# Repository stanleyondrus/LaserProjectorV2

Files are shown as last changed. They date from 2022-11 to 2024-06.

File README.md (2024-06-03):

(https://stanleyprojects.com/projects/laserprojector_v2/)
(https://stanleyprojects.com/projects/laserprojector_v2/)

## Introduction
LaserProjector V2 is a battery-powered, ESP32-based laser XY scanner using stepper motors to deflect the beam. It has auto-homing functionality, and can be controlled wirelessly (Wi-Fi & Bluetooth).

## Features
- Hybrid Wi-Fi operation mode (STA & AP)
- Webserver GUI with custom WebSocket protocol
- Concurrent multi-user control
- Automatic/Manual/External scanning mode
- Parallel auto-homing
- Battery-powered

## Links
- [Documentation [stanleyprojects.com]](https://stanleyprojects.com/projects/laserprojector_v2/)
- [Article [hackaday.com]](https://hackaday.com/2022/11/02/laser-project-relies-on-steppers-rather-than-galvanometers/)
- [Video [youtube.com]](https://youtu.be/w1O48Ysdiiw)
- [Project [hackaday.io]](https://hackaday.io/project/188046-laserprojector-v2)
- [Project [hackster.io]](https://www.hackster.io/stanleyprojects/laserprojector-v2-fa77cf)

## Design




## How to build your own release
### Prerequisites
- Visual Studio Code with PlatformIO extension
- 3.3V USB to Serial (e.g. FT232RL)
### Building
1. Open __*firmware/src*__ folder in VSCode
2. In __*firmware/src/src/main.cpp*__ you can sustomize SSID and PASSWORD for Wi-Fi STA mode:
```cpp
const char* ssid = "<your_ssid>";
const char* password = "<your_pass>";
```
3. In __*firmware/src/platformio.ini*__ set the correct *_upload_port_*, or remove to auto-detect.

4. Build and upload the filesystem
    - PlatformIO > esp32serial > Platform > Build Filesystem Image
    - PlatformIO > esp32serial > Platform > Upload Filesystem Image

5. Build and upload the firmware
    - PlatformIO > esp32serial > General > Upload

## Pre-built binaries
The binary is fully contained (bootloader, firmware, and filesystem), so it can be flashed to address 0x0.

The easiest way is to use this web tool: https://stanleyprojects.com/projects/laserprojector_v2/install

After the firmware is loaded, any subsequent updates can be done OTA in browser by visiting _http://\<esp32-ip-address\>/update_

|Version|Firmware|
|-|-|
|0.1|[LaserProjectorV2_firmware_v0.1.bin](https://github.com/stanleyondrus/LaserProjectorV2/releases/download/v0.1/LaserProjectorV2_v0.1.bin)|

## Credits
- [A Beginner's Guide to the ESP8266](https://tttapa.github.io/ESP8266/Chap01%20-%20ESP8266.html)
- [ElegantOTA](https://github.com/ayushsharma82/ElegantOTA)
- [StepperDriver](https://github.com/laurb9/StepperDriver)

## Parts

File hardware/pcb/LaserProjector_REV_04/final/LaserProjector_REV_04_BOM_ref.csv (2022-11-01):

Ref | Value | MPN | Manufacturer | Package | Datasheet
C1 | 2.2uF | GRM188R61H225KE11D | Murata Electronics | 0603 | https://datasheet.lcsc.com/lcsc/1912111437_Murata-Electronics-GRM188R61H225KE11D_C162273.pdf
C2 | 22uF | EEEHBH220UAP | Panasonic | SMD (6.3x5.8mm) | https://datasheet.lcsc.com/lcsc/1912111437_PANASONIC-EEEHBH220UAP_C401821.pdf
C3 | 10uF | CL21A106KAYNNNE | Samsung Electro-Mechanics | 0805 | https://datasheet.lcsc.com/szlcsc/1811121310_Samsung-Electro-Mechanics-CL21A106KAYNNNE_C15850.pdf
C4 | 22uF | C2012X5R0J226MT000N | TDK | 0805 | https://datasheet.lcsc.com/szlcsc/1912111437_TDK-C2012X5R0J226MT000N_C329961.pdf
C5 | 1nF | GCM155R71H102KA37D | Murata Electronics | 0402 | https://datasheet.lcsc.com/lcsc/1811081510_Murata-Electronics-GCM155R71H102KA37D_C126532.pdf
C6 | 22nF | GRM155R71E223JA61D | Murata Electronics | 0402 | https://datasheet.lcsc.com/lcsc/1912111437_Murata-Electronics-GRM155R71E223JA61D_C426639.pdf
C7 | 100nF | CC0402KRX7R7BB104 | Yageo | 0402 | https://www.yageo.com/upload/media/product/productsearch/datasheet/mlcc/UPY-GPHC_X7R_6.3V-to-50V_18.pdf
C8 | 2.2uF | GRM188R61H225KE11D | Murata Electronics | 0603 | https://datasheet.lcsc.com/lcsc/1912111437_Murata-Electronics-GRM188R61H225KE11D_C162273.pdf
C9 | 22uF | EEEHBH220UAP | Panasonic | SMD (6.3x5.8mm) | https://datasheet.lcsc.com/lcsc/1912111437_PANASONIC-EEEHBH220UAP_C401821.pdf
C10 | 1nF | GCM155R71H102KA37D | Murata Electronics | 0402 | https://datasheet.lcsc.com/lcsc/1811081510_Murata-Electronics-GCM155R71H102KA37D_C126532.pdf
C11 | 22nF | GRM155R71E223JA61D | Murata Electronics | 0402 | https://datasheet.lcsc.com/lcsc/1912111437_Murata-Electronics-GRM155R71E223JA61D_C426639.pdf
J1 | J_Molex-PicoBlade-4P-P1.25mm | 0530470410 | Molex | Through Hole, P=1.25mm | https://www.molex.com/pdm_docs/sd/530470410_sd.pdf
J2 | JST-XH-B2B | B2B-XH-A(LF)(SN) | JST Sales America | Through Hole, P=2.5mm | http://www.jst-mfg.com/product/pdf/eng/eXH.pdf
J3 | J_Molex-PicoBlade-3P-P1.25mm | 0530470310 | Molex | Through Hole, P=1.25mm | https://www.molex.com/pdm_docs/sd/530470310_sd.pdf
J4 | J_Molex-PicoBlade-3P-P1.25mm | 0530470310 | Molex | Through Hole, P=1.25mm | https://www.molex.com/pdm_docs/sd/530470310_sd.pdf
J5 | JST-XH-B4B | B4B-XH-A(LF)(SN) | JST Sales America | Through Hole, P=2.5mm | https://datasheet.lcsc.com/szlcsc/1811151545_JST-Sales-America-B4B-XH-A-LF-SN_C144395.pdf
J7 | J_Molex-PicoBlade-4P-P1.25mm | 0530470410 | Molex | Through Hole, P=1.25mm | https://www.molex.com/pdm_docs/sd/530470410_sd.pdf
L1 | 2.2uH | VLCF4020T-2R2N1R7 | TDK | 4x4x2mm | https://datasheet.lcsc.com/szlcsc/1810211523_TDK-VLCF4020T-2R2N1R7_C136245.pdf
Q1 | NCE2060K | NCE2060K | Wuxi NCE Power Semiconductor | TO-252-2L | http://www.ncepower.com/Upload/MOSFET/NCE2060Kdatasheet-15115513193.pdf
Q2 | NMOS | NTR4501NT1G | ON Semicon | SOT-23 | https://datasheet.lcsc.com/szlcsc/1810301530_ON-Semicon-NTR4501NT1G_C85416.pdf
R1 | 0.2R | WW25WR200FTL | Walsin Tech Corp | 2512 | https://datasheet.lcsc.com/lcsc/1912211104_Walsin-Tech-Corp-WW25WR200FTL_C470051.pdf
R2 | 47k | RC0402FR-0747KL | Yageo | 0402 | https://www.mouser.dk/datasheet/2/447/PYu_RC_Group_51_RoHS_L_10-1664068.pdf
R3 | 0.2R | WW25WR200FTL | Walsin Tech Corp | 2512 | https://datasheet.lcsc.com/lcsc/1912211104_Walsin-Tech-Corp-WW25WR200FTL_C470051.pdf
R4 | 100k | RT0402BRE07100KL | YAGEO | 0402 | https://datasheet.lcsc.com/lcsc/1810241324_YAGEO-RT0402BRE07100KL_C136979.pdf
R5 | 1k | 0402WGF1001TCE | Uniroyal Elec | 0402 | https://datasheet.lcsc.com/szlcsc/1811132311_Uniroyal-Elec-0402WGF1001TCE_C11702.pdf
R6 | 1k | 0402WGF1001TCE | Uniroyal Elec | 0402 | https://datasheet.lcsc.com/szlcsc/1811132311_Uniroyal-Elec-0402WGF1001TCE_C11702.pdf
R7 | 10k | RT0402BRD0710KL | YAGEO | 0402 | https://datasheet.lcsc.com/szlcsc/1810241334_YAGEO-RT0402BRD0710KL_C190095.pdf
R8 | 10k | RT0402BRD0710KL | YAGEO | 0402 | https://datasheet.lcsc.com/szlcsc/1810241334_YAGEO-RT0402BRD0710KL_C190095.pdf
R9 | 0.2R | WW25WR200FTL | Walsin Tech Corp | 2512 | https://datasheet.lcsc.com/lcsc/1912211104_Walsin-Tech-Corp-WW25WR200FTL_C470051.pdf
R10 | 47k | RC0402FR-0747KL | Yageo | 0402 | https://www.mouser.dk/datasheet/2/447/PYu_RC_Group_51_RoHS_L_10-1664068.pdf
R11 | 0.2R | WW25WR200FTL | Walsin Tech Corp | 2512 | https://datasheet.lcsc.com/lcsc/1912211104_Walsin-Tech-Corp-WW25WR200FTL_C470051.pdf
R12 | 100k | RT0402BRE07100KL | YAGEO | 0402 | https://datasheet.lcsc.com/lcsc/1810241324_YAGEO-RT0402BRE07100KL_C136979.pdf
R13 | 1k | 0402WGF1001TCE | Uniroyal Elec | 0402 | https://datasheet.lcsc.com/szlcsc/1811132311_Uniroyal-Elec-0402WGF1001TCE_C11702.pdf
R14 | 1k | 0402WGF1001TCE | Uniroyal Elec | 0402 | https://datasheet.lcsc.com/szlcsc/1811132311_Uniroyal-Elec-0402WGF1001TCE_C11702.pdf
R15 | 10k | RT0402BRD0710KL | YAGEO | 0402 | https://datasheet.lcsc.com/szlcsc/1810241334_YAGEO-RT0402BRD0710KL_C190095.pdf
SW1 | EVPAA602W | EVPAA602W | Panasonic | SMD | https://datasheet.lcsc.com/szlcsc/1809192044_PANASONIC-EVPAA602W_C79148.pdf
SW2 | EVPAA602W | EVPAA602W | Panasonic | SMD | https://datasheet.lcsc.com/szlcsc/1809192044_PANASONIC-EVPAA602W_C79148.pdf
U1 | TPS62162DSG | TPS62162DSG | Texas Instruments | WSON-8 (2x2mm) | https://datasheet.lcsc.com/lcsc/1806070425_Texas-Instruments-TPS62162DSGR_C40256.pdf
U2 | STSPIN220 | STSPIN220 | STMicroelectronics | VFQFPN 3x3x1.0 | www.st.com/resource/en/datasheet/stspin220.pdf
U3 | STSPIN220 | STSPIN220 | STMicroelectronics | VFQFPN 3x3x1.0 | www.st.com/resource/en/datasheet/stspin220.pdf
U4 | ESP32 |  |  |  | https://www.espressif.com/sites/default/files/documentation/esp32-wroom-32_datasheet_en.pdf

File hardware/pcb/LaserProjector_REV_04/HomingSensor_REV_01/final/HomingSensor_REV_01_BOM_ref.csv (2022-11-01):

Ref | Value | MPN | Manufacturer | Package | Datasheet
C1 | 10nF | CL05B103KB5NNNC | Samsung Electro-Mechanics | 0402 | https://datasheet.lcsc.com/szlcsc/1810191223_Samsung-Electro-Mechanics-CL05B103KB5NNNC_C15195.pdf
R1 | 100R | AC0402FR-07100RL | Yageo | 0402 | https://eu.mouser.com/datasheet/2/447/PYu-AC_51_RoHS_L_7-1714230.pdf
R2 | 220R | 0402WGF2200TCE | UNI-ROYAL | 0402 | https://datasheet.lcsc.com/szlcsc/1811011214_UNI-ROYAL-Uniroyal-Elec-0402WGF2200TCE_C25091.pdf
U1 | QRE1113 |  |  |  | http://www.onsemi.com/pub/Collateral/QRE1113-D.PDF

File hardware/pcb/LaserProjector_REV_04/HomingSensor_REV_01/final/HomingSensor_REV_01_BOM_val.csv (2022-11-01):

Qty | Designator | Value | Datasheet | MPN | Manufacturer | Package
1 | C1 | 10nF | https://datasheet.lcsc.com/szlcsc/1810191223_Samsung-Electro-Mechanics-CL05B103KB5NNNC_C15195.pdf | Samsung Electro-Mechanics | CL05B103KB5NNNC | 0402
1 | R1 | 100R | https://eu.mouser.com/datasheet/2/447/PYu-AC_51_RoHS_L_7-1714230.pdf | Yageo | AC0402FR-07100RL | 0402
1 | R2 | 220R | https://datasheet.lcsc.com/szlcsc/1811011214_UNI-ROYAL-Uniroyal-Elec-0402WGF2200TCE_C25091.pdf | UNI-ROYAL | 0402WGF2200TCE | 0402
1 | U1 | QRE1113 | http://www.onsemi.com/pub/Collateral/QRE1113-D.PDF

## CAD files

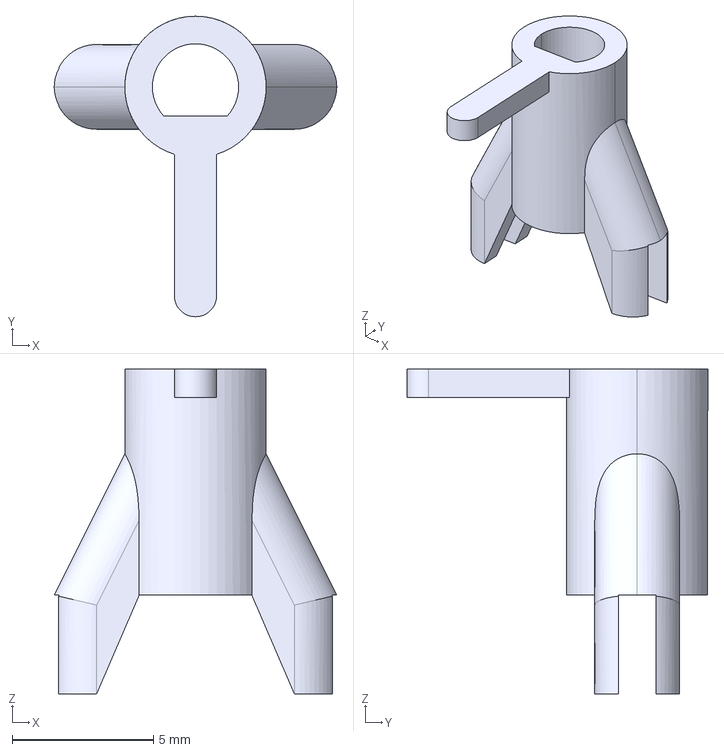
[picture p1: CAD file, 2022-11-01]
hardware/cad/MirrorHolder.STEP
10.0 x 10.6 x 11.5 mm

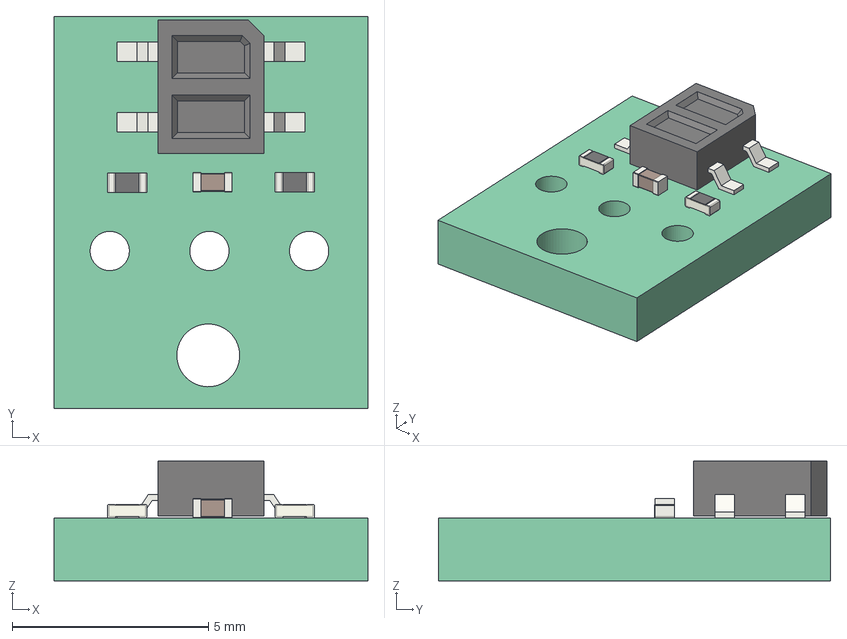
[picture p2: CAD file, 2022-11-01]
hardware/pcb/LaserProjector_REV_04/HomingSensor_REV_01/final/HomingSensor_REV_01.step
8.00 x 10.0 x 3.05 mm
Local_CS_25fb
Pcb_25fb
PCB_Sketch_25fb
U1_OnSemi_CASE100CY_5FA408A3
R2_R_0402_1005Metric_5FA4088F
R1_R_0402_1005Metric_5FA40D70
C1_C_0402_1005Metric_5FA4085A

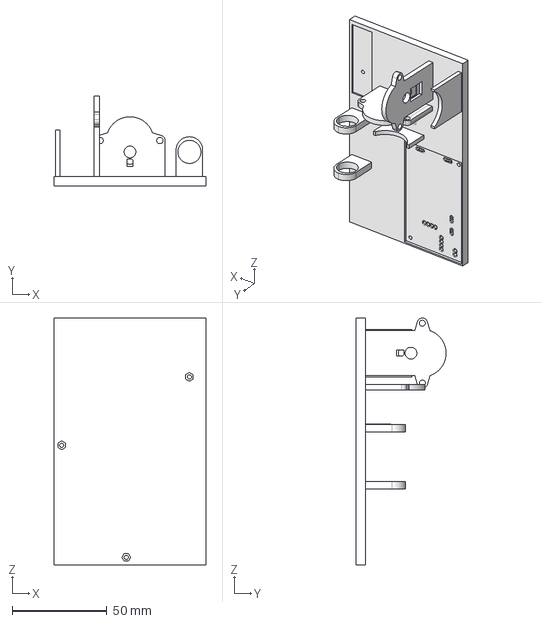
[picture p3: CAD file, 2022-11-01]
hardware/cad/ScannerHolder.STEP
80.0 x 47.5 x 130.0 mm

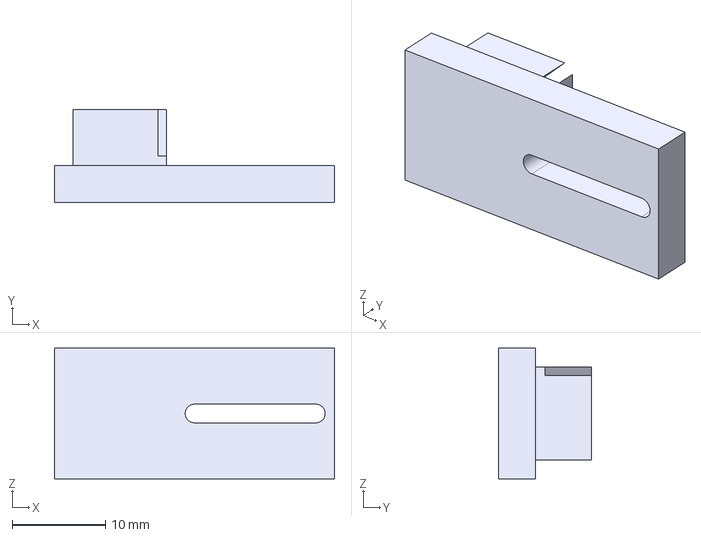
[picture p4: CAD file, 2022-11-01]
hardware/cad/BeamAligner.STEP
30.0 x 10.0 x 14.0 mm

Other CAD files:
hardware/cad/BeamAligner.STL
hardware/cad/MirrorHolder.STL
hardware/cad/ScannerHolder.STL

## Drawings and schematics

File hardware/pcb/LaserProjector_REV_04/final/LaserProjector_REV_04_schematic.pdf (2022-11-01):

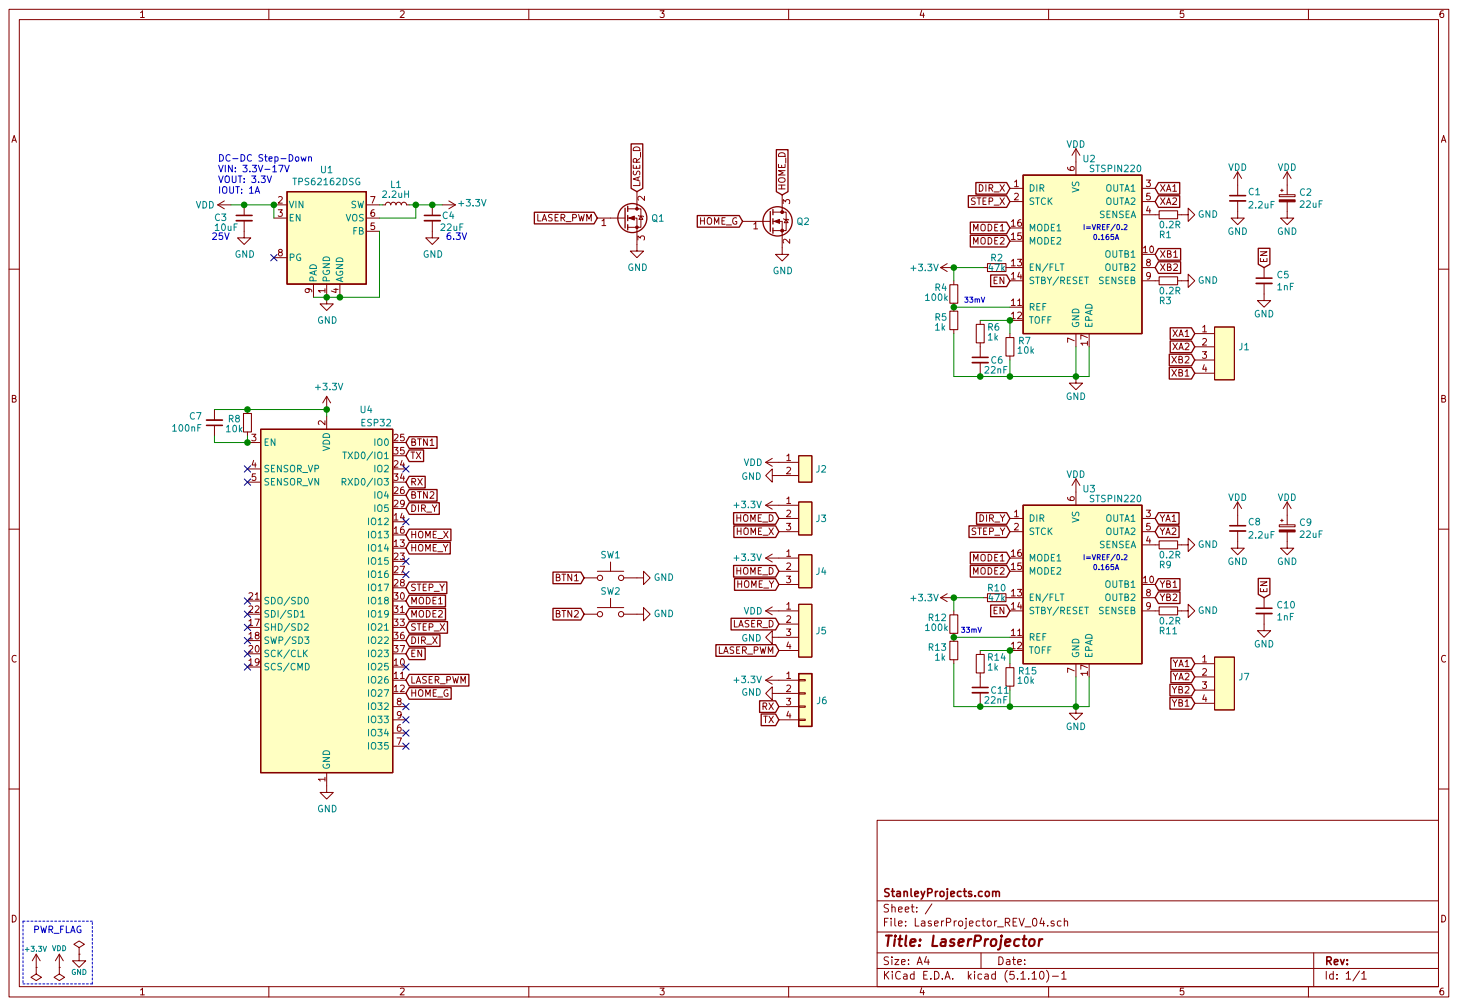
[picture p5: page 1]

DC-DC Step-Down VIN: 3.3V-17V

4 FB 5 VOS 6 SW 7 PG 8 PAD

2 SCK/CLK 20 SDO/SD0 21 SDI/SD1 22
TXHOME_Y HOME_G

File: LaserProjector_REV_04.sch Sheet: / StanleyProjects.com

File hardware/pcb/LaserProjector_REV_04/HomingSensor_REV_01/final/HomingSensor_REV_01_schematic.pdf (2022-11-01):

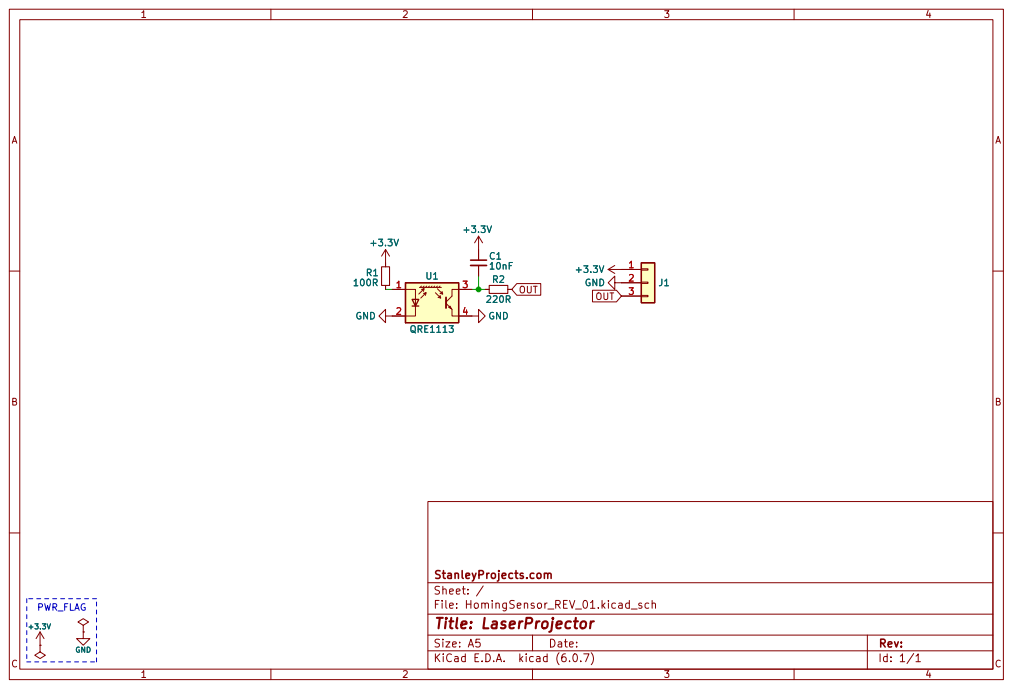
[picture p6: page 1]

File: HomingSensor_REV_01.kicad_sch Sheet: / StanleyProjects.com

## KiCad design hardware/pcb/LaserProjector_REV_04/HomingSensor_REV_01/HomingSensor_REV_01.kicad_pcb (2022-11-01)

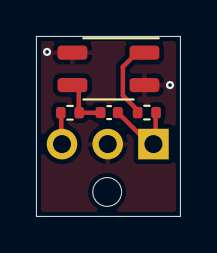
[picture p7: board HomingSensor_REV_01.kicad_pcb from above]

Board: 2 copper layers, 8.0 x 10.0 mm, 5 parts (1 on the bottom side), 5 nets.

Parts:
C1: 10nF; C_0402_1005Metric
J2: Connector; PinSocket_1x03_P2.54mm_Vertical
R1: 100R; R_0402_1005Metric
R2: 220R; R_0402_1005Metric
U1: QRE1113; OnSemi_CASE100CY

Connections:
+3V3: C1.1, J2.1, R1.2
GND: J2.2, U1.2, U1.4
unnamed: C1.2, R2.2, U1.3
unnamed: R1.1, U1.1
OUT: J2.3, R2.1

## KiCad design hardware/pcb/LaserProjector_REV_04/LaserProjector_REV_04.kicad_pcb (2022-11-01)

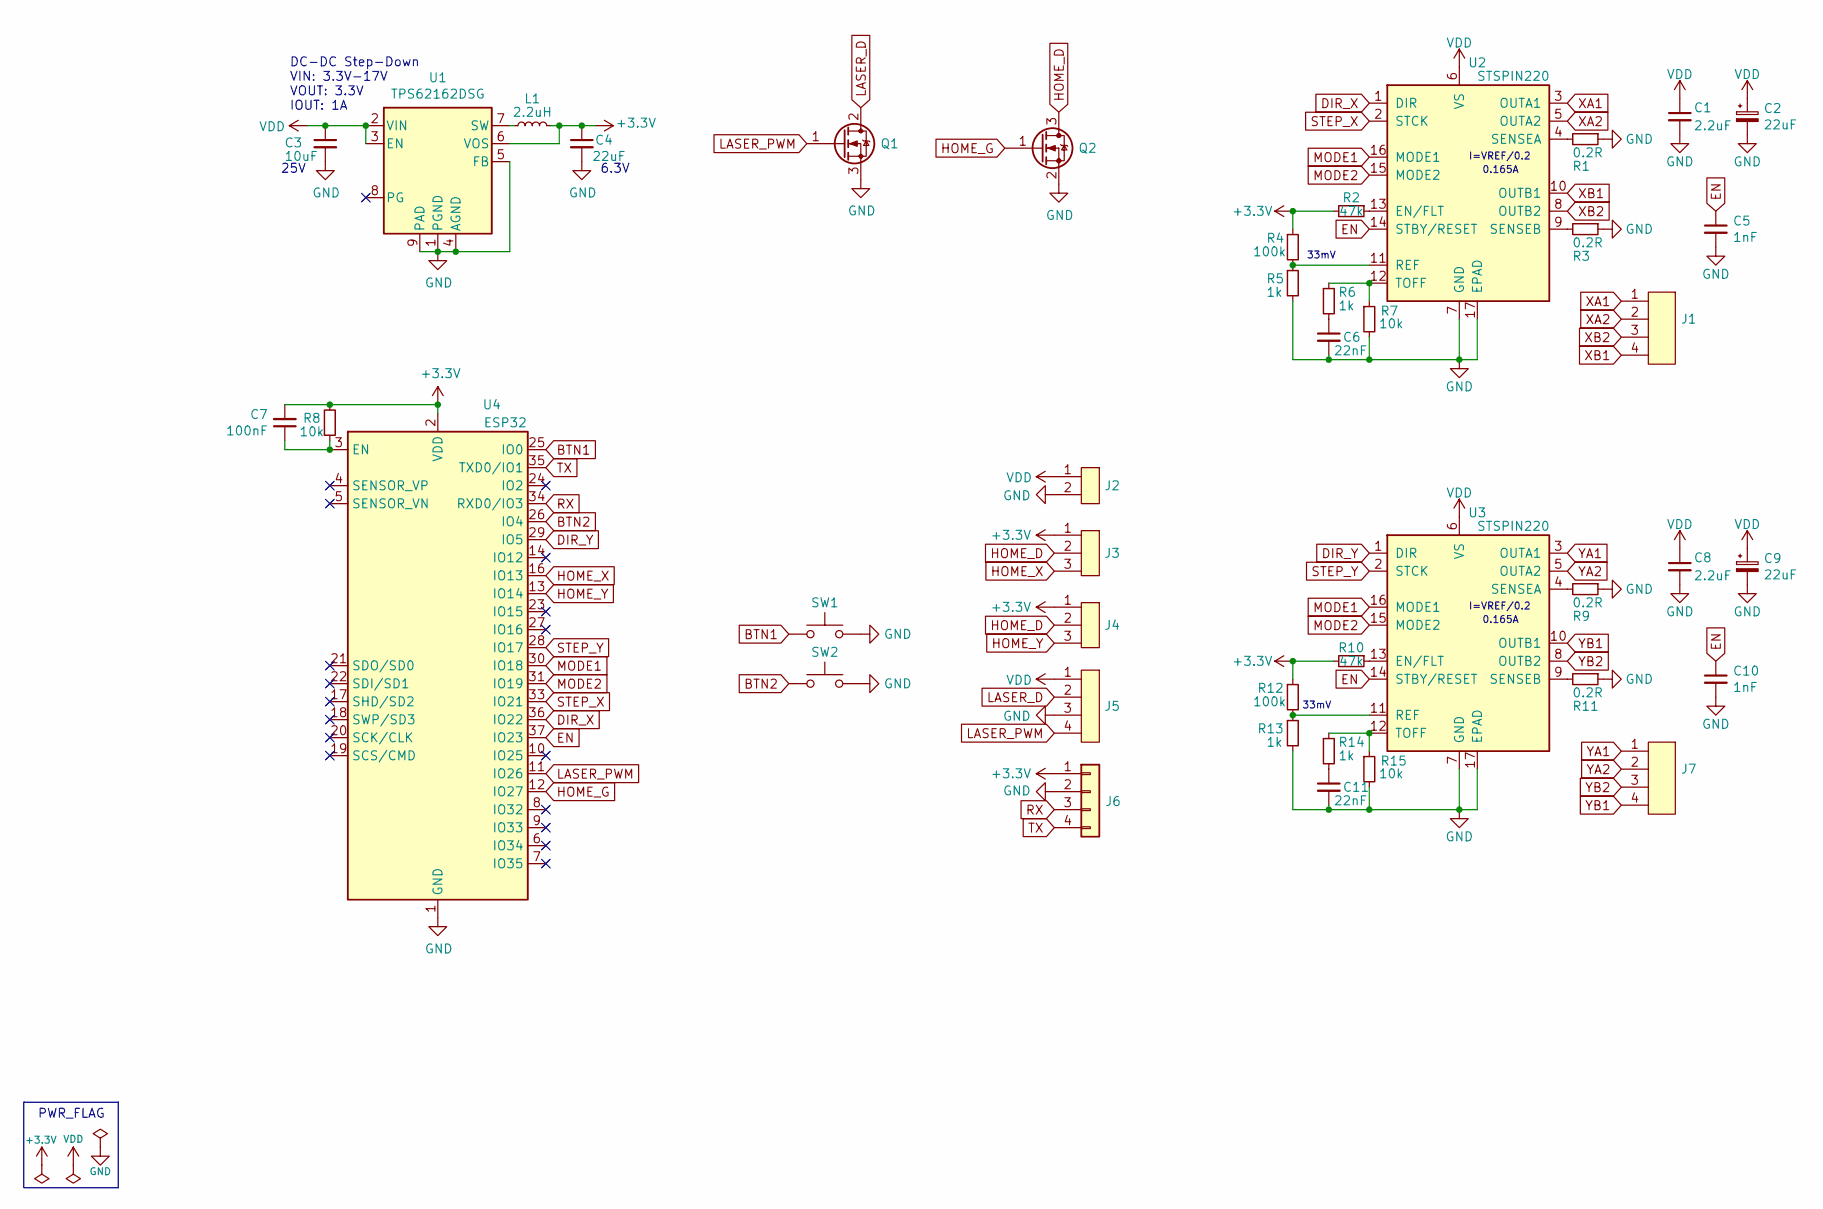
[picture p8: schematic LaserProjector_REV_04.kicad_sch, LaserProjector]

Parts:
C1, C8: 2.2uF; C_0603_1608Metric; MPN GRM188R61H225KE11D
C2, C9: 22uF; CP_Elec_6.3x5.8; MPN EEEHBH220UAP
C3: 10uF; C_0805_2012Metric; MPN CL21A106KAYNNNE
C4: 22uF; C_0805_2012Metric; MPN C2012X5R0J226MT000N
C5, C10: 1nF; C_0402_1005Metric; MPN GCM155R71H102KA37D
C6, C11: 22nF; C_0402_1005Metric; MPN GRM155R71E223JA61D
C7: 100nF; C_0402_1005Metric; MPN CC0402KRX7R7BB104
J1, J7: J_Molex-PicoBlade-4P-P1.25mm; Molex_PicoBlade_53047-0410_1x04_P1.25mm_Vertical; MPN 0530470410
J2: JST-XH-B2B; JST_XH_B2B-XH-A_1x02_P2.50mm_Vertical; MPN B2B-XH-A(LF)(SN)
J3, J4: J_Molex-PicoBlade-3P-P1.25mm; Molex_PicoBlade_53047-0310_1x03_P1.25mm_Vertical; MPN 0530470310
J5: JST-XH-B4B; JST_XH_B4B-XH-A_1x04_P2.50mm_Vertical; MPN B4B-XH-A(LF)(SN)
J6: Conn_01x04; PinHeader_1x04_P2.54mm_Vertical
L1: 2.2uH; VLCF4020; MPN VLCF4020T-2R2N1R7
Q1: NCE2060K; TO-252-2; MPN NCE2060K
Q2: NMOS; SOT-23; MPN NTR4501NT1G
R1, R3, R9, R11: 0.2R; R_2512_6332Metric; MPN WW25WR200FTL
R2, R10: 47k; R_0402_1005Metric; MPN RC0402FR-0747KL
R4, R12: 100k; R_0402_1005Metric; MPN RT0402BRE07100KL
R5, R6, R13, R14: 1k; R_0402_1005Metric; MPN 0402WGF1001TCE
R7, R8, R15: 10k; R_0402_1005Metric; MPN RT0402BRD0710KL
SW1, SW2: EVPAA602W; SW_EVPAA; MPN EVPAA602W
U1: TPS62162DSG; WSON-8-1EP_2x2mm_P0.5mm_EP0.9x1.6mm_ThermalVias; MPN TPS62162DSG
U2, U3: STSPIN220; MPN STSPIN220
U4: ESP32; ESP32-WROOM-32

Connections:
+3V3: C4.1, C7.2, J3.1, J4.1, J6.1, L1.2, R2.2, R4.1, R8.2, R10.2, R12.1, U1.6 (VOS), U4.2 (VDD)
BTN1: SW1.1, SW1.3, U4.25 (IO0); also elsewhere on the board
BTN2: SW2.1, SW2.3, U4.26 (IO4); also elsewhere on the board
DIR_X: U2.1 (DIR), U4.36 (IO22)
DIR_Y: U3.1 (DIR), U4.29 (IO5)
EN: C5.1, C10.1, U2.14 (STBY/RESET), U3.14 (STBY/RESET), U4.37 (IO23)
GND: C1.2, C2.2, C3.2, C4.2, C5.2, C6.2, C8.2, C9.2, C10.2, C11.2, J2.2, J5.3, J6.2, Q1.3 (S), Q2.2 (S), R1.1, R3.1, R5.2, R7.2, R9.1, R11.1, R13.2, R15.2, SW1.2, SW1.4, SW2.2, SW2.4, U1.1 (PGND), U1.4 (AGND), U1.5 (FB), U1.8 (PG), U1.9 (PAD), U2.7 (GND), U2.17 (EPAD), U3.7 (GND), U3.17 (EPAD), U4.1 (GND), U4.15 (GND), U4.38 (GND), U4.39 (GND); also elsewhere on the board
HOME_D: J3.2, J4.2, Q2.3 (D)
HOME_G: Q2.1 (G), U4.12 (IO27)
HOME_X: J3.3, U4.16 (IO13)
HOME_Y: J4.3, U4.13 (IO14)
LASER_D: J5.2, Q1.2 (D)
LASER_PWM: J5.4, Q1.1 (G), U4.11 (IO26)
MODE1: U2.16 (MODE1), U3.16 (MODE1), U4.30 (IO18)
MODE2: U2.15 (MODE2), U3.15 (MODE2), U4.31 (IO19)
unnamed: C6.1, R6.2
unnamed: C7.1, R8.1, U4.3 (EN)
unnamed: C11.1, R14.2
unnamed: L1.1, U1.7 (SW)
unnamed: R1.2, U2.4 (SENSEA)
unnamed: R2.1, U2.13 (EN/FLT)
unnamed: R3.2, U2.9 (SENSEB)
unnamed: R4.2, R5.1, U2.11 (REF)
unnamed: R6.1, R7.1, U2.12 (TOFF)
unnamed: R9.2, U3.4 (SENSEA)
unnamed: R10.1, U3.13 (EN/FLT)
unnamed: R11.2, U3.9 (SENSEB)
unnamed: R12.2, R13.1, U3.11 (REF)
unnamed: R14.1, R15.1, U3.12 (TOFF)
RX: J6.3, U4.34 (RXD0/IO3)
STEP_X: U2.2 (STCK), U4.33 (IO21)
STEP_Y: U3.2 (STCK), U4.28 (IO17)
TX: J6.4, U4.35 (TXD0/IO1)
VDD: C1.1, C2.1, C3.1, C8.1, C9.1, J2.1, J5.1, U1.2 (VIN), U1.3 (EN), U2.6 (VS), U3.6 (VS)
XA1: J1.1, U2.3 (OUTA1)
XA2: J1.2, U2.5 (OUTA2)
XB1: J1.4, U2.10 (OUTB1)
XB2: J1.3, U2.8 (OUTB2)
YA1: J7.1, U3.3 (OUTA1)
YA2: J7.2, U3.5 (OUTA2)
YB1: J7.4, U3.10 (OUTB1)
YB2: J7.3, U3.8 (OUTB2)

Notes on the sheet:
0.165A
PWR_FLAG
25V
6.3V
33mV
I=VREF/0.2
DC-DC Step-Down VIN: 3.3V-17V VOUT: 3.3V IOUT: 1A

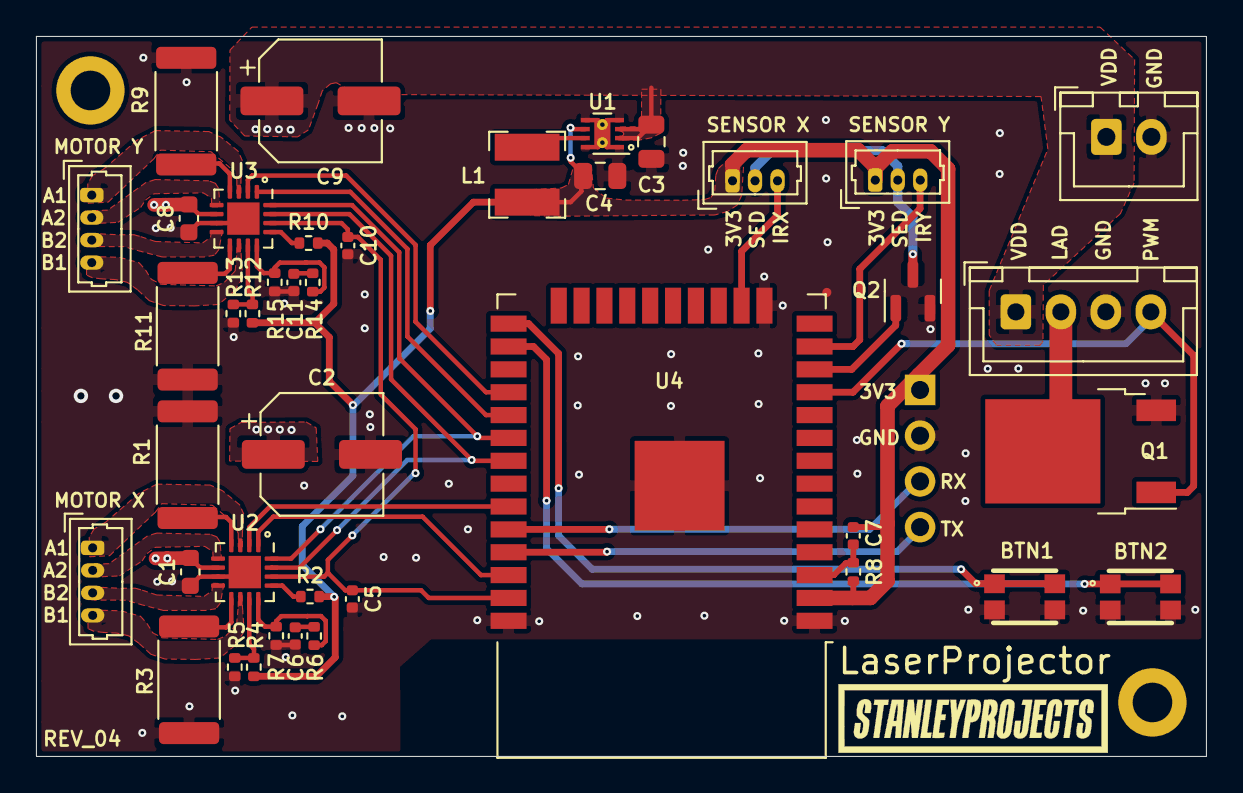
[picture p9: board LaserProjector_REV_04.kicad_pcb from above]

Board: 2 copper layers, 65.0 x 40.0 mm, 42 parts (0 on the bottom side), 42 nets.

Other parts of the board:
BTN1, BTN2: EVPAA602W; SW_EVPAA

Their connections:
BTN1: BTN1.1, BTN1.3; also elsewhere on the board
BTN2: BTN2.1, BTN2.3; also elsewhere on the board
GND: BTN1.2, BTN1.4, BTN2.2, BTN2.4; also elsewhere on the board

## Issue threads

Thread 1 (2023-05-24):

Availability of 25GBCT2 stepper motor

twitchyliquid64, 2023-05-24:
I was wondering if you had any remaining sources you knew of for the stepper you used? I couldn't find it on aliexpress, I even went to the same seller as the page in your video.

Have you tried the more common 28BYJ-48 motors? My guess is the reduction in those is a little too high / motor is too slow to draw lines?

twitchyliquid64, 2023-05-24:
Thats a shame :/ I'll try and find a replacement. You mentioned briefly in the video that NEMA stepper motors weren't ideal: was that because of the weight being too much to move quickly or not having enough stepping granularity?

Also, were you microstepping the 25GBCT2's? Your code has `#define MICROSTEPS 1` but then seems to pull both mode pins low, which i thought was a full-step mode?

stanleyondrus, 2023-05-24:
Not really sure what the problem was but I wasn't able to get sufficient torque at high speed.
Defining MICROSTEPS 1 basically means full-step mode. To use microstepping, set it to 4,8,16,..., and pull the mode pins to corresponding values.

twitchyliquid64, 2023-10-06:
The A or B configurations of these boiz might be ideal?

https://www.aliexpress.us/item/3256803023172572.html

Considering buying a bunch and giving them a go.

lucalutz2005-dev, 2023-10-11:
First of all awesome project, very nice!
Would be very nice to find a good replacement motor. I am also interested in building this laser projector myself.

twitchyliquid64, 2023-10-14:
Apparently the B configuration (1:42 ratio) yields a step angle of 0.43 degrees, so that might work?

(I messaged the seller)

stanleyondrus, 2023-10-17:
I would probably go for geared assemblies based on 15mm GM12-15BY (like the one @twitchyliquid64) or smaller 10mm GM12-10BY stepper motors. They have a step angle of 18° (20 steps per revolution), so even with 1:21 gearing ratio, you would get 18°/21=0.857° step angle.

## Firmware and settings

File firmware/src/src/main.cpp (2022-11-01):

#include <Arduino.h>
#include <WiFi.h>
#include "ESPAsyncWebServer.h"
#include "LittleFS.h"
#include <AsyncElegantOTA.h>

#include "ScannerDriver.h"
#include "HomingDriver.h"
#include "LaserDriver.h"
#include "AnimLib.h"

#define FW_VER_MAJ 0
#define FW_VER_MIN 1

#define BTN1 0 // GPIO0
#define BTN2 4 // GPIO4

AsyncWebServer server(80);
AsyncWebSocket ws("/ws");

#define FORMAT_LITTLEFS_IF_FAILED false

HomingDriver hd;
ScannerDriver scanner(hd);
LaserDriver laser;
AnimLib anim(scanner, laser);

const char* ssid = "<your_ssid>";
const char* password = "<your_pass>";

const char* soft_ap_ssid = "LaserProjector";
const char* soft_ap_password = "LaserProjector2020";

char incoming_packet[30];
uint8_t process_flag = 0;

unsigned long last_btn_press = 0;

void sendStatus() {
    // M[0-3] - Mode [OFF,MAN,AUT,EXT]
    // L[0-255] - Laser intensity
    // P[1-20] - Preset (used when M1)
    // S[1-2] - Scaling (used when M1)
    // V[1-3] - Speed (used when M1)
    // C0[0-Xmax,0-Ymax,0-1] - Current position, laser [X,Y,Laser]

    char s[50];
    sprintf(s, "M%u;L%u;P%u;S%u;V%u;C0%u,%u,%u\0", anim.getMode(), laser.getIntensity(), anim.getPreset(), anim.getScaling(), scanner.getSpeed(), scanner.getX(), scanner.getY(), laser.getState());

    ws.textAll(s); // notify WebSocket clients
    Serial.println(s); // notify Serial clients
}

void handleIncomingPackets() {
    // Handle Serial
    if (Serial.available()) {
        uint8_t counter = 0;
        while (Serial.available() && counter < 30) {
            incoming_packet[counter++] = Serial.read();
        }
        incoming_packet[counter] = '\0';
        process_flag = 1;
    }
}

void parseMessage(char* msg) {
    // R - Request status
    // H - Home steppers
    // M[0-3] - Set mode [OFF,MAN,AUT,EXT]
    // L[0-255] - Set laser intensity
    // P[1-20] - Set preset (applicable when M1)
    // S[1-2] - Set scaling (applicable when M1)
    // V[1-3] - Set speed (applicable when M1)
    // C0[0-Xmax,0-Ymax,0-1] - External control [X,Y,Laser]
    // C1[0-Xmax,0-Ymax] - External control [X,Y]
    // C2[0-1] - External control [Laser On, Laser Off]
    // Z - Request FW version

    if (msg[0] == 'R'); // Do nothing, just send status
    else if (msg[0] == 'H') {
        if (anim.getMode() == 1 || anim.getMode() == 2) anim.setMode(anim.getMode());
        else anim.home();
    }
    else if (msg[0] == 'M') {
        anim.setMode(atoi(msg + 1));
    }
    else if (msg[0] == 'L') {
        uint8_t intensity = atoi(msg + 1);
        laser.setMaxIntensity(intensity);
    }
    else if (msg[0] == 'P') {
        anim.setPreset(atoi(msg + 1));
    }
    else if (msg[0] == 'S') {
        anim.setScaling(atoi(msg + 1));
    }
    else if (msg[0] == 'V') {
        scanner.setSpeed(atoi(msg + 1));
    }
    else if (msg[0] == 'C') {
        if (msg[1] == '0') {
            char* ctrpacket = strtok(msg + 2, ",");
            uint8_t i = 0;
            uint16_t x = 0;
            uint16_t y = 0;
            uint8_t l = 0;
            while (ctrpacket != 0) {
                if (i == 0) x = atoi(ctrpacket);
                if (i == 1) y = atoi(ctrpacket);
                if (i == 2) l = atoi(ctrpacket);
                ctrpacket = strtok(0, ";"); // search for another
                i++;
            }
            laser.setState(l);
            scanner.setState(1);
            scanner.move(x, y);
            scanner.setState(0);
        }
        else if (msg[1] == '1') {
            char* ctrpacket = strtok(msg + 2, ",");
            uint8_t i = 0;
            uint16_t x = 0;
            uint16_t y = 0;
            while (ctrpacket != 0) {
                if (i == 0) x = atoi(ctrpacket);
                if (i == 1) y = atoi(ctrpacket);
                ctrpacket = strtok(0, ";"); // search for another
                i++;
            }
            scanner.setState(1);
            scanner.move(x, y);
            scanner.setState(0);
        }
        else if (msg[1] == '2') {
            laser.setState((uint8_t)atoi(msg + 2));
        }
    }
    else if (msg[0] == 'D') {
        scanner.home_offset_x = atoi(msg + 1);
        Serial.print(scanner.home_offset_x);
        Serial.print("\t");
        Serial.println(scanner.home_offset_y);
    }
    else if (msg[0] == 'E') {
        scanner.home_offset_y = atoi(msg + 1);
        Serial.print(scanner.home_offset_x);
        Serial.print("\t");
        Serial.println(scanner.home_offset_y);
    }
    else if (msg[0] == 'F') {
        anim.test_anim_x = atoi(msg + 1);
        Serial.print(anim.test_anim_x);
        Serial.print("\t");
        Serial.println(anim.test_anim_y);
    }
    else if (msg[0] == 'G') {
        anim.test_anim_y = atoi(msg + 1);
        Serial.print(anim.test_anim_x);
        Serial.print("\t");
        Serial.println(anim.test_anim_y);
    }
    else if (msg[0] == 'Z') {
        char s[10];
        sprintf(s, "Z%d.%d;", FW_VER_MAJ, FW_VER_MIN);
        ws.textAll(s);
    }
}

void processIncomingPacket() {
    if (process_flag == 0) return;
    char* packet = strtok((char*)incoming_packet, ";"); // split on ;
    while (packet != 0) {
        // Serial.println(packet);
        parseMessage(packet);
        packet = strtok(0, ";"); // search for another
    }
    sendStatus();
    process_flag = 0;
}

void onWsEvent(AsyncWebSocket* server, AsyncWebSocketClient* client, AwsEventType type, void* arg, uint8_t* data, size_t len) {
    switch (type) {
    case WS_EVT_CONNECT:
        Serial.printf("WebSocket client #%u connected from %s\n", client->id(), client->remoteIP().toString().c_str());
        break;
    case WS_EVT_DISCONNECT:
        Serial.printf("WebSocket client #%u disconnected\n", client->id());
        break;
    case WS_EVT_DATA:
    {
        AwsFrameInfo* info = (AwsFrameInfo*)arg;
        // Serial.printf("ws[%s][%u] %s-message[%llu]: ", server->url(), client->id(), (info->opcode == WS_TEXT) ? "text" : "binary", info->len);
        if (info->final && info->index == 0 && info->len == len && info->opcode == WS_TEXT) {
            data[len] = 0;
            strcpy(incoming_packet, (char*)data);
            process_flag = 1;
        }
        break;
    }
    case WS_EVT_ERROR:
        Serial.printf("ws[%s][%u] error(%u): %s\n", server->url(), client->id(), *((uint16_t*)arg), (char*)data);
        break;
    case WS_EVT_PONG:
        Serial.printf("ws[%s][%u] pong[%u]: %s\n", server->url(), client->id(), len, (len) ? (char*)data : "");
        break;
    }
}

uint8_t btnPressed(uint8_t pin) {
    return !digitalRead(pin);
}

void handleBtn() {
    // BTN1 pressed + BTN2 to change modes 0-2
    // BTN1 2s hold to mode 0 
    if (btnPressed(BTN1)) last_btn_press = millis();
    while (btnPressed(BTN1)) {
        laser.setState(0);
        if (btnPressed(BTN2)) {
            uint8_t next_mode = anim.getMode() + 1;
            if (next_mode > 2) next_mode = 0;
            anim.setMode(next_mode);
        }
        while (btnPressed(BTN2));
        if (millis() - last_btn_press >= 2000) {
            anim.setMode(0);
        }
    }

    if (btnPressed(BTN2)) {
        // In MAN mode, BTN2 to increment preset
        if (anim.getMode() == 1) {
            uint8_t next_preset = anim.getPreset() + 1;
            if (next_preset > anim.total_presets) next_preset = 1;
            anim.setPreset(next_preset);
            while (btnPressed(BTN2));
        }
        else anim.home();
    }

    last_btn_press = millis();
}

void setup() {
    Serial.begin(115200);

    Serial.println("LaserProjector V2");
    Serial.print("FW VER: ");
    Serial.print(FW_VER_MAJ);
    Serial.print(".");
    Serial.println(FW_VER_MIN);

    pinMode(BTN1, INPUT_PULLUP);
    pinMode(BTN2, INPUT_PULLUP);

    laser.init();
    hd.init();
    scanner.init();

    randomSeed(analogRead(2));

    if (!LittleFS.begin(FORMAT_LITTLEFS_IF_FAILED)) {
        Serial.println("LittleFS Mount Failed");
        return;
    }

    WiFi.mode(WIFI_MODE_APSTA);
    WiFi.softAP(soft_ap_ssid, soft_ap_password);
    WiFi.begin(ssid, password);

    unsigned long timeout = millis();
    Serial.print("Connecting to ");
    Serial.println(ssid);
    while (WiFi.status() != WL_CONNECTED && (millis() - timeout < 3000)) {
        Serial.print(".");
        delay(500);
    }
    Serial.println(WiFi.localIP());
    Serial.println(WiFi.softAPIP());

    ws.onEvent(onWsEvent);
    server.addHandler(&ws);

    server.on("/", HTTP_GET, [](AsyncWebServerRequest* request) {
        request->send(LittleFS, "/index.html", "text/html", false);
    });

    server.serveStatic("/", LittleFS, "/");

    AsyncElegantOTA.begin(&server);

    server.begin();
}

void loop() {
    ws.cleanupClients();
    handleBtn();
    handleIncomingPackets();
    processIncomingPacket();
    anim.update();
}

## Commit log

2016-03-31 [LaserControl.exe] fixed error when connecting to the wrong COM port [ArduinoLaserScanner.ino] ability to start/stop auto-mode remotely (star-pattern/STOP button while switch in auto-mode)
2017-08-28 LaserControl Source Code
2022-11-01 LaserProjector V2 - init
    [BeamAligner.STEP, BeamAligner.STL, HomingSensor_REV_01.kicad_pcb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]
